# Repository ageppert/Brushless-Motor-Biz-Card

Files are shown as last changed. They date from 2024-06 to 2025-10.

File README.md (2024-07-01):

# Brushless-Motor-Biz-Card
Wind your own brushless motor and experiment in the form factor of a business card!

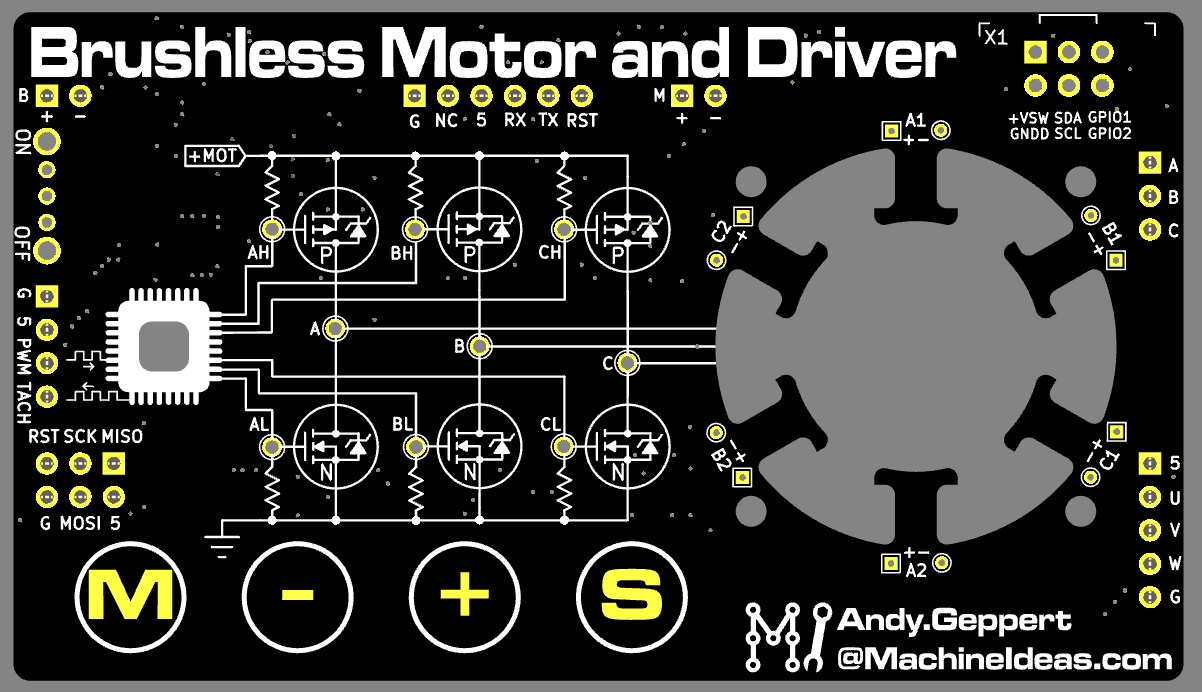
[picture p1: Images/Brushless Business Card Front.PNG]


Follow this project at: https://hackaday.io/project/196576-brushless-motor-and-driver-business-card-kit

# Hardware Version History (latest on top)

HWV0.1 - Prototypes

# REFERENCES

Carl Bugeja - PCB Motors and related magical creations

https://www.youtube.com/@CarlBugeja

Random Access Projects - Open loop brushless motor and beyond

https://www.youtube.com/channel/UCRd9x4pmbc09_RXTrkSY2Gg

Electronoobs - brushless motor and ESC projects

https://www.youtube.com/@ELECTRONOOBS

SimpleFOC Project

https://simplefoc.com/

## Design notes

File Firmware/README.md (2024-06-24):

# Firmware Development

Arduino IDE

5V FTDI-USB Cable

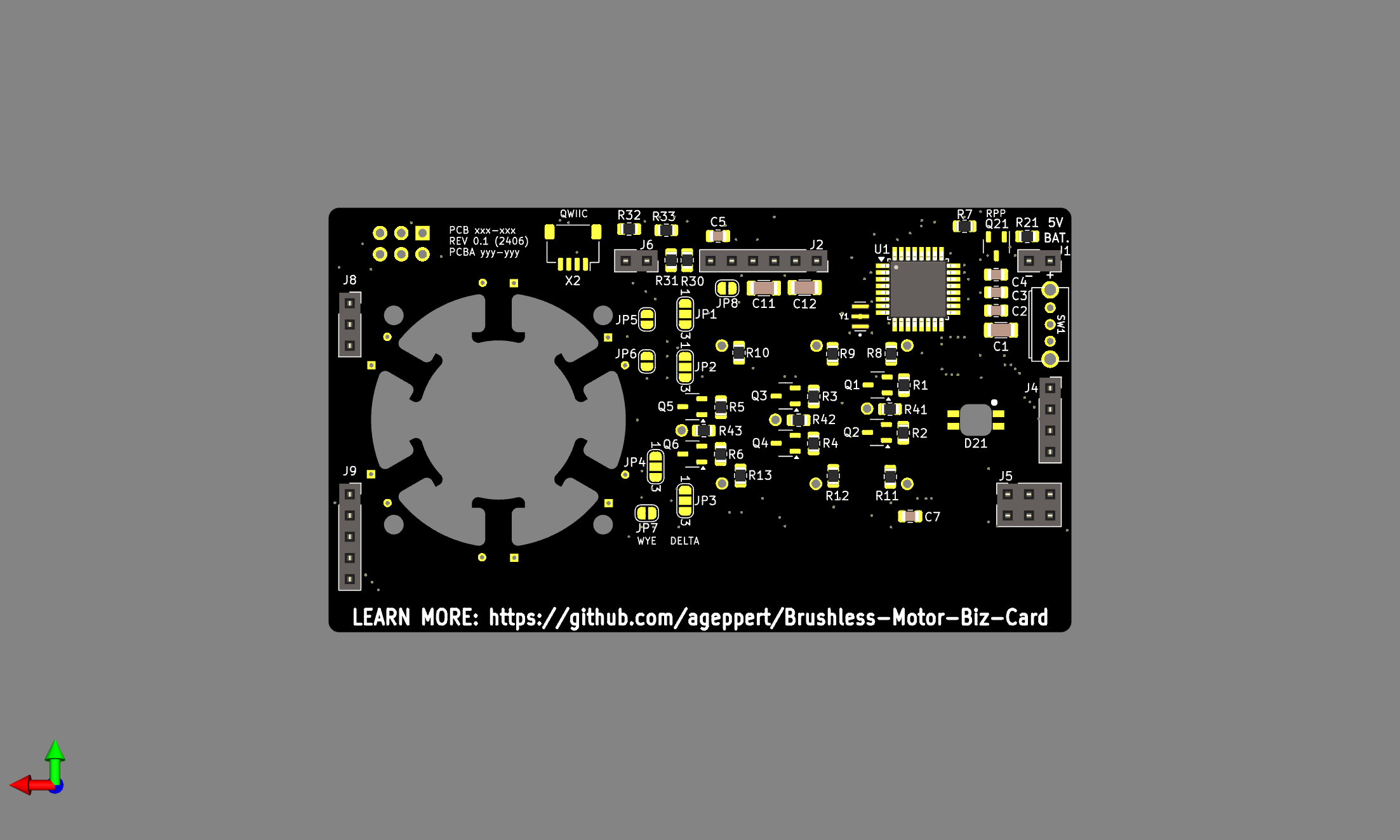
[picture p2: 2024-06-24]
Electronics/BLDC_BIZ_CARD_V0.1 Schematic and Renders/BLDC_BIZ_CARD_render back.png

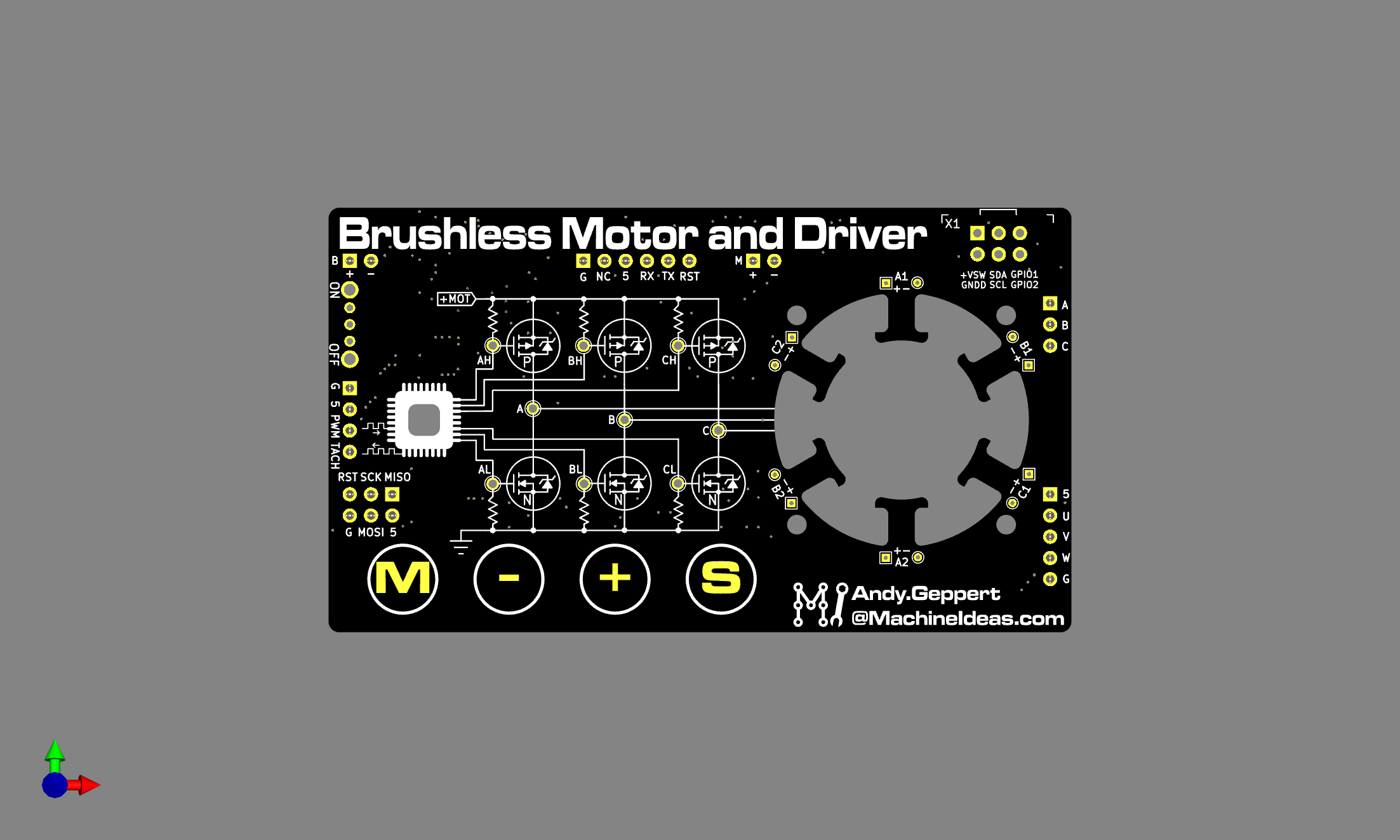
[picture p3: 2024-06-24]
Electronics/BLDC_BIZ_CARD_V0.1 Schematic and Renders/BLDC_BIZ_CARD_render front.png

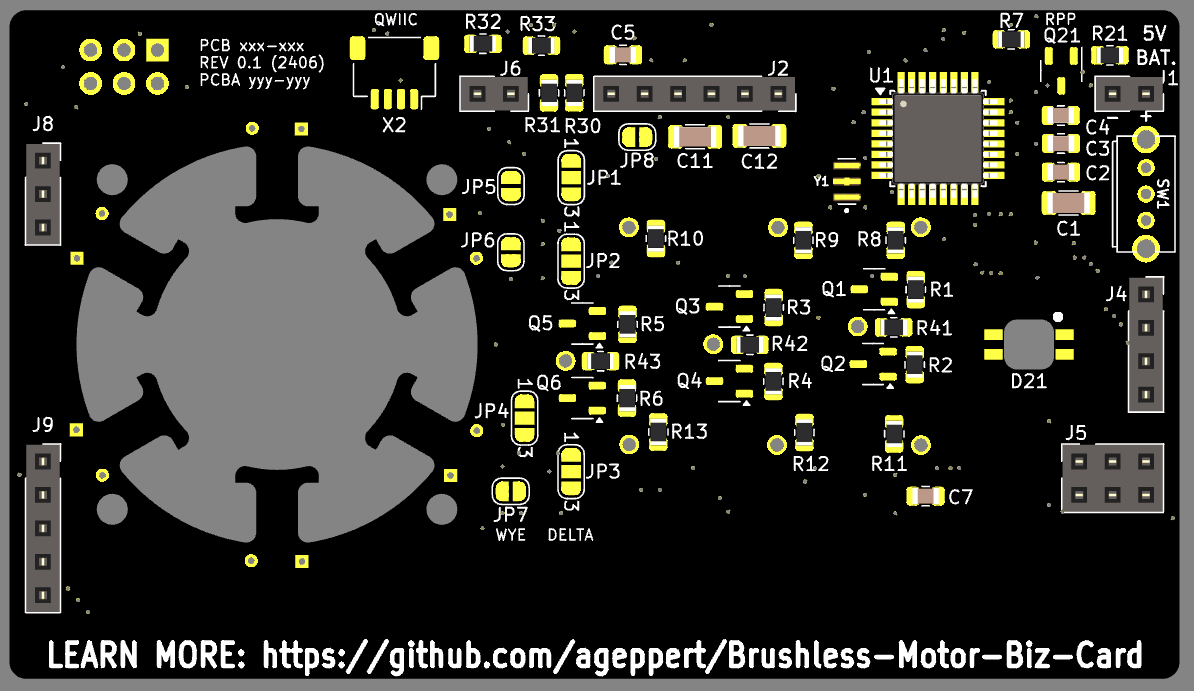
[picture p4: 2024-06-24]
Images/Brushless Business Card Back.PNG

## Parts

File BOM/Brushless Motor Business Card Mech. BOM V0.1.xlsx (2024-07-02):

Brushless Motor and Driver Business Card
Designed by Andy Geppert, www.MachineIdeas.com
Revision 0.1
Mechanical BOM
NAME | DESCRIPTION | QUANTITY | NOTES | LINK
Business Card PCBA | Circuit Board Assembly | 1 | Order a PCB from PCBWAY or JLCPCB with the Gerbers Order the components in the Electrical BOM folder | https://github.com/ageppert/Brushless-Motor-Biz-Card/
Rotor 8P | 3D Print, PETG 0.2mm layers, 20% infill | 1 | DIY, JLCPCB, PCBWAY, etc. | https://cad.onshape.com/documents/f519e018cd04a070474f7458/w/7211a2b8f86f81003258f57c/e/c9c6c988519f346738a797cf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
Motor Support | 3D Print, PETG 0.2mm layers, 20% infill | 4 | DIY, JLCPCB, PCBWAY, etc. | https://cad.onshape.com/documents/f519e018cd04a070474f7458/w/7211a2b8f86f81003258f57c/e/c9c6c988519f346738a797cf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
Winder | 3D Print, PETG 0.2mm layers, 20% infill | 1 | DIY, JLCPCB, PCBWAY, etc. | https://cad.onshape.com/documents/f519e018cd04a070474f7458/w/7211a2b8f86f81003258f57c/e/c9c6c988519f346738a797cf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
Magnet | D22 Cylinder, 1/8" x 1/8" N42, NI. Axial Magnetization | 8 |  | https://www.kjmagnetics.com/proddetail.asp?prod=D22
Bearing | 681X 681X-ZZ Miniature Bearings Mini Open Bearing 1.5 x 4 x 1.2mm | 2 |  | https://www.amazon.com/gp/product/B07HSP9YZ8/
Axle | Brass Rod,Brass Solid Round Rod 0.7mm/0.027inch Diameter, 200mm | 1 | Cut to 0.30 inches | https://www.amazon.com/gp/product/B0B665P1KF
Magnet Wire | 32 AWG enamel or Polyamideimide coating wire | 25 ft | 130 wraps per coil, all coils wind clockwise | https://www.remingtonindustries.com/magnet-wire/magnet-wire-200c-32-awg-polyamideimide-7-spool-sizes/
Screw | M2 x 6mm Phillips head | 4 | Screw assortment comes in handy for other projects! | https://www.amazon.com/gp/product/B0BP6P37QY/

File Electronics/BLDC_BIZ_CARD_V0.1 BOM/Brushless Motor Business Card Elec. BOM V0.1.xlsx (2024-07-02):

Brushless Motor and Driver Business Card
Designed by Andy Geppert, www.MachineIdeas.com
Revision 0.1
REF. DES. | VALUE | FOOTPRINT | QUANTITY | DNP | DIGIKEY PN | MFR PN | OTHER
> C1, C11, C12 | 220uF | Capacitor_SMD:C_1206_3216Metric | 3 |  | 490-13970-1-ND | GRM31CR60J227ME11L
C2 | 10uF | Capacitor_SMD:C_0805_2012Metric | 1 |  | 1276-6472-1-ND | CL21B106KOQNNNG
> C3-C5, C7 | 0.1uF | Capacitor_SMD:C_0805_2012Metric | 4 |  | 1276-2922-1-ND | CL21B104KAFNNNE
D21 | SK6812 | Core_64_footprints:4960_ADA_REV_RGB_LED_short_pads | 1 |  | 1528-4960-ND | SK6812-E
J1 | BATTERY | Connector_PinSocket_2.54mm:PinSocket_1x02_P2.54mm_Vertical | 1 |  | See OTHER |  | Any 0.1" header pins such as: https://www.amazon.com/Header-Lystaii-Pin-Connector-Electronic/dp/B06ZZN8L9S/ https://www.amazon.com/Yohii-Single-Right-Header-Connector/dp/B07C89T16T/
J2 | Conn_01x06_SER_PROG | Connector_PinSocket_2.54mm:PinSocket_1x06_P2.54mm_Vertical | 1 |  | See OTHER
> J4, J9 | Conn_01x04 | -- mixed values -- | 2 |  | See OTHER
J5 | Conn_02x03_Odd_Even_ISP | Connector_PinSocket_2.54mm:PinSocket_2x03_P2.54mm_Vertical | 1 |  | See OTHER
J6 | Conn_01x02_MOTOR_POWER | Connector_PinSocket_2.54mm:PinSocket_1x02_P2.54mm_Vertical | 1 |  | See OTHER
J8 | Conn_01x03 | Connector_PinSocket_2.54mm:PinSocket_1x03_P2.54mm_Vertical | 1 |  | See OTHER
> Q1, Q3, Q5, Q21 | Q_PMOS_GSD | Package_TO_SOT_SMD:SOT-23-3 | 4 |  | DMP2066LSNDICT-ND | DMP2066LSN-7
> Q2, Q4, Q6 | Q_NMOS_GSD | Package_TO_SOT_SMD:SOT-23-3 | 3 |  | DMN2020LSN-7DICT-ND | DMN2020LSN-7
> R1-R6, R41-R43 | 1K | Resistor_SMD:R_0805_2012Metric | 9 |  | 2019-RK73H2ATTD1001FCT-ND | RK73H2ATTD1001F
> R7, R21 | 10K | Resistor_SMD:R_0805_2012Metric | 2 |  | 2019-RK73H2ATTD1002FCT-ND | RK73H2ATTD1002F
> R8-R13 | 470 | Resistor_SMD:R_0805_2012Metric | 6 |  | 2019-RK73H2ATTD4700FCT-ND | RK73H2ATTD4700F
> R30, R31 | 1K2 | Resistor_SMD:R_0805_2012Metric | 2 |  | 2019-RK73H2ATTD1201FCT-ND | RK73H2ATTD1201F
> R32, R33 | 68 | Resistor_SMD:R_0805_2012Metric | 2 |  | 2019-RK73H2ATTD68R0FCT-ND | RK73H2ATTD68R0F
SW1 | SK12D07L4B | BLDC_BIZ_CARD_Footprints:SK12D07VG4 | 1 |  | CKN9559-ND | OS102011MA1QN1
U1 | ATmega328PB-A | Package_QFP:TQFP-32_7x7mm_P0.8mm | 1 |  | ATMEGA328PB-AU-ND | ATMEGA328PB-AU
X1 | SAO_Header | BLDC_BIZ_CARD_Footprints:Badgelife-SAOv169-BADGE-2x3 | 1 |  | S9717-ND | SFH11-NBPC-D03-ST-BK
X2 | QWIIC | Connector_JST:JST_SH_SM04B-SRSS-TB_1x04-1MP_P1.00mm_Horizontal | 1 |  | 455-SM04B-SRSS-TBTR-ND | SM04B-SRSS-TB
Y1 | 16MHz 15pF Resonator | BLDC_BIZ_CARD_Footprints:OSC_CSTNE20M0V53Z000R0 | 1 |  | 490-17950-1-ND | CSTNE16M0V53Z000R0

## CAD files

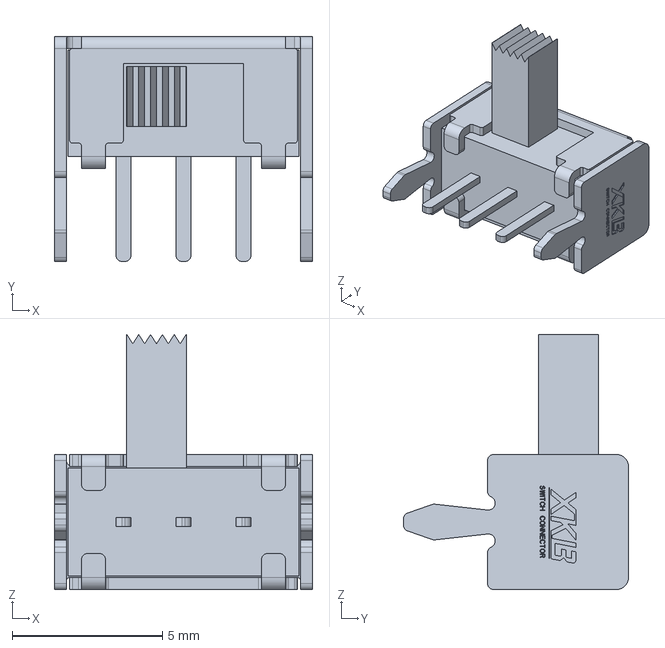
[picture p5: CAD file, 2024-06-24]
Electronics/BLDC_BIZ_CARD_Footprints/SK12D07L4B.stp
8.60 x 7.50 x 8.50 mm

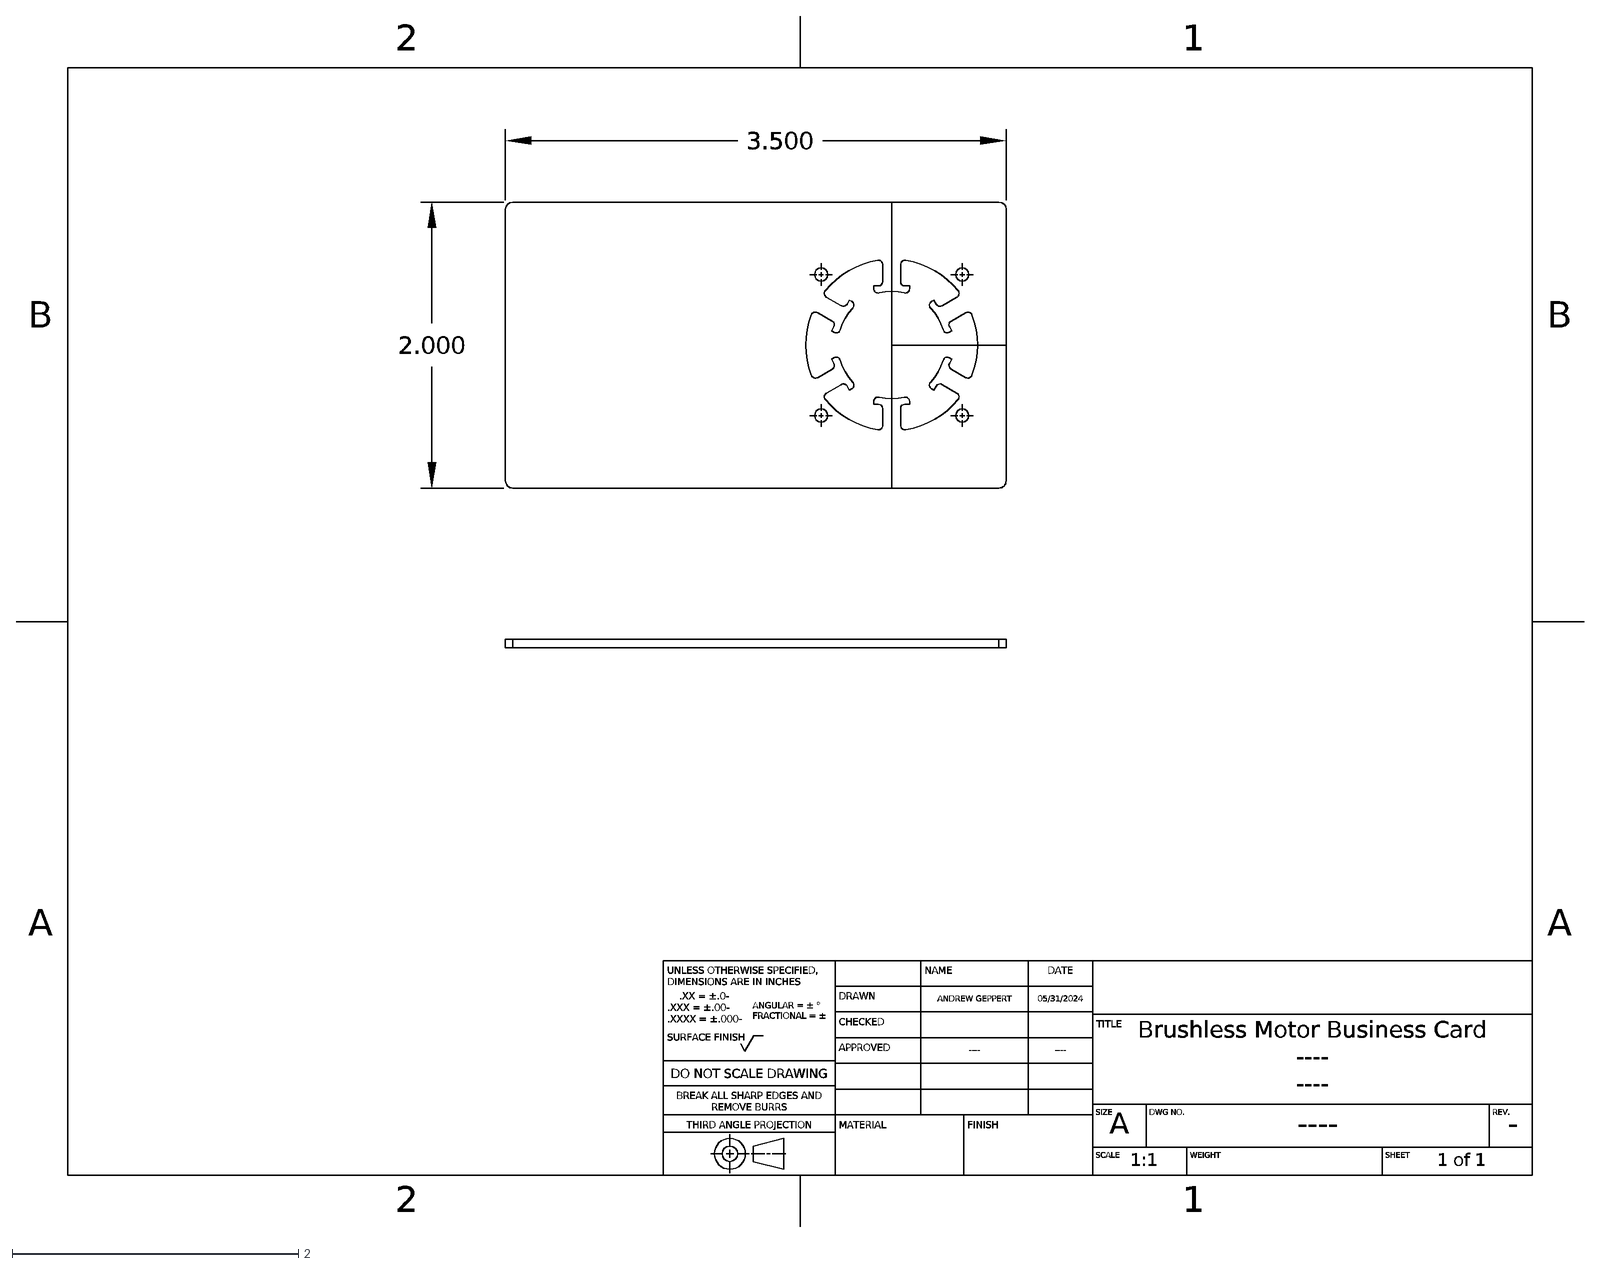
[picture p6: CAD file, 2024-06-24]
Graphics/Card and winding outline.dxf
2
1
A
B
UNLESS OTHERWISE SPECIFIED, DIMENSIONS ARE IN INCHES
.XX = ±.0- .XXX = ±.00- .XXXX = ±.000-
ANGULAR = ± ° FRACTIONAL = ±
SURFACE FINISH
DO NOT SCALE DRAWING
BREAK ALL SHARP EDGES AND REMOVE BURRS
THIRD ANGLE PROJECTION
NAME
DATE
DRAWN
ANDREW GEPPERT
05/31/2024
CHECKED
APPROVED
----
MATERIAL
FINISH
TITLE
Brushless Motor Business Card
SIZE
DWG NO.
REV.
-
SCALE
1:1
WEIGHT
SHEET
1 of 1
3.500
2.000

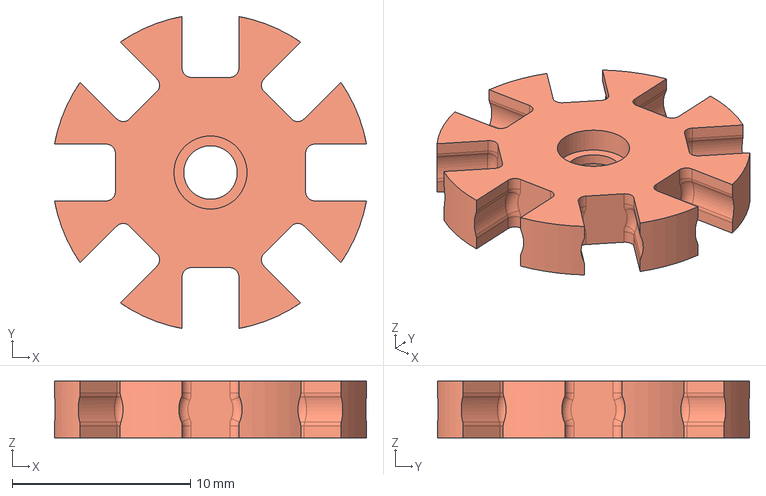
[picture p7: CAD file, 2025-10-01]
Mechanical/Rotor 8P V1.step
17.5 x 17.5 x 3.17 mm

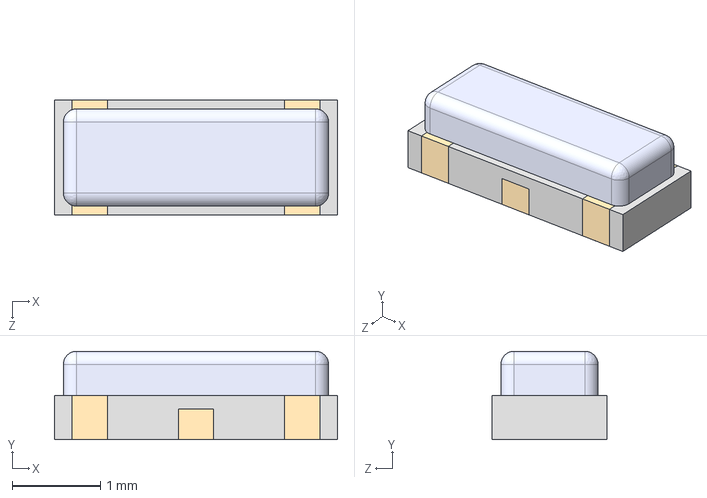
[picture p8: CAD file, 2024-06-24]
Electronics/BLDC_BIZ_CARD_Footprints/OSC_CSTNE20M0V53Z000R0.step
3.20 x 1.00 x 1.30 mm

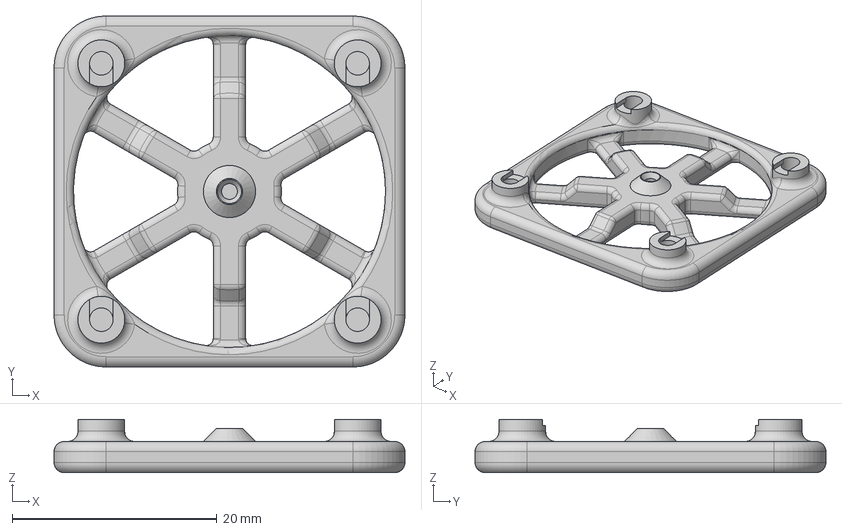
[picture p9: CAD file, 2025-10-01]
Mechanical/Motor Support V1.step
34.3 x 34.3 x 5.21 mm

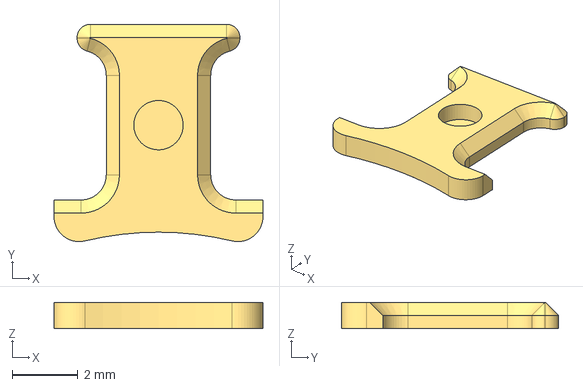
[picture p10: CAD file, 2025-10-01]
Mechanical/Winding Spacer V1.step
6.35 x 6.60 x 0.794 mm

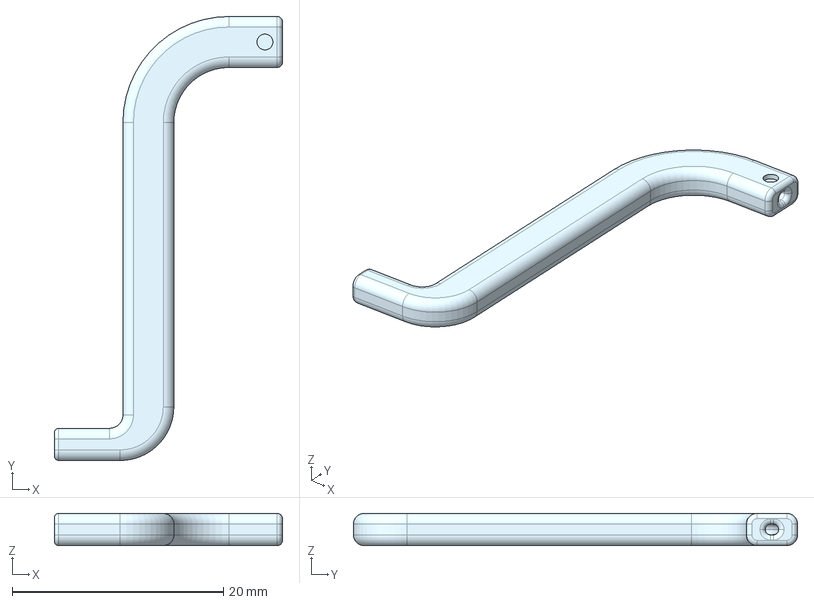
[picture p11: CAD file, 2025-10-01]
Mechanical/Winder V1.step
21.6 x 42.0 x 3.05 mm

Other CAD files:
Mechanical/Motor Support V1.stl
Mechanical/Rotor 8P V1.stl
Mechanical/Winder V1.stl
Mechanical/Winding Spacer V1.stl

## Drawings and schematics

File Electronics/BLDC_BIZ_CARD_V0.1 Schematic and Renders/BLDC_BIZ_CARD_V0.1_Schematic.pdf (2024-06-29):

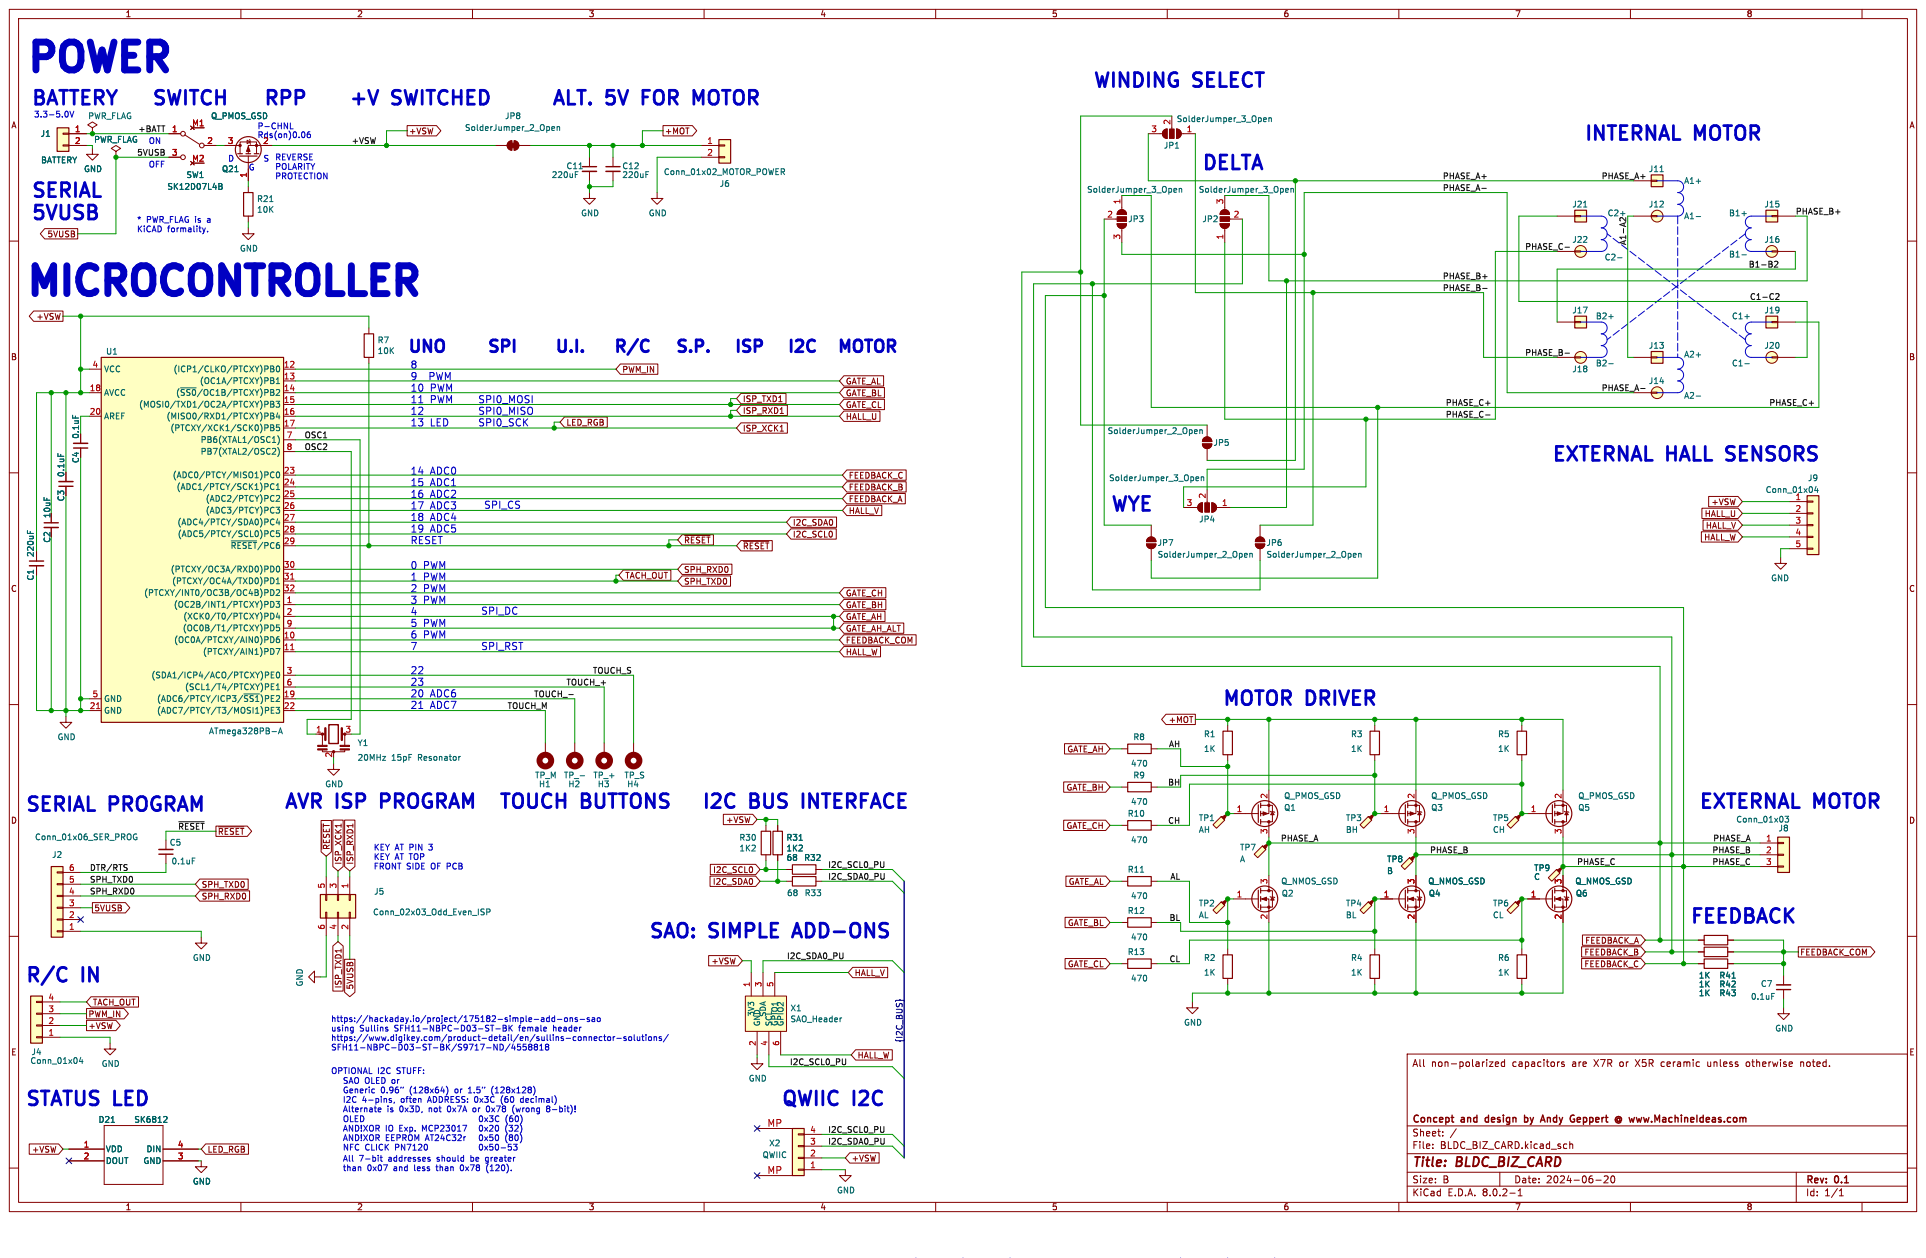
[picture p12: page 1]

KEY AT PIN 3 KEY AT TOP

https://hackaday.io/project/175182-simple-add-ons-sao

AND!XOR IO Exp. MCP23017 AND!XOR EEPROM AT24C32r NFC CLICK PN7120

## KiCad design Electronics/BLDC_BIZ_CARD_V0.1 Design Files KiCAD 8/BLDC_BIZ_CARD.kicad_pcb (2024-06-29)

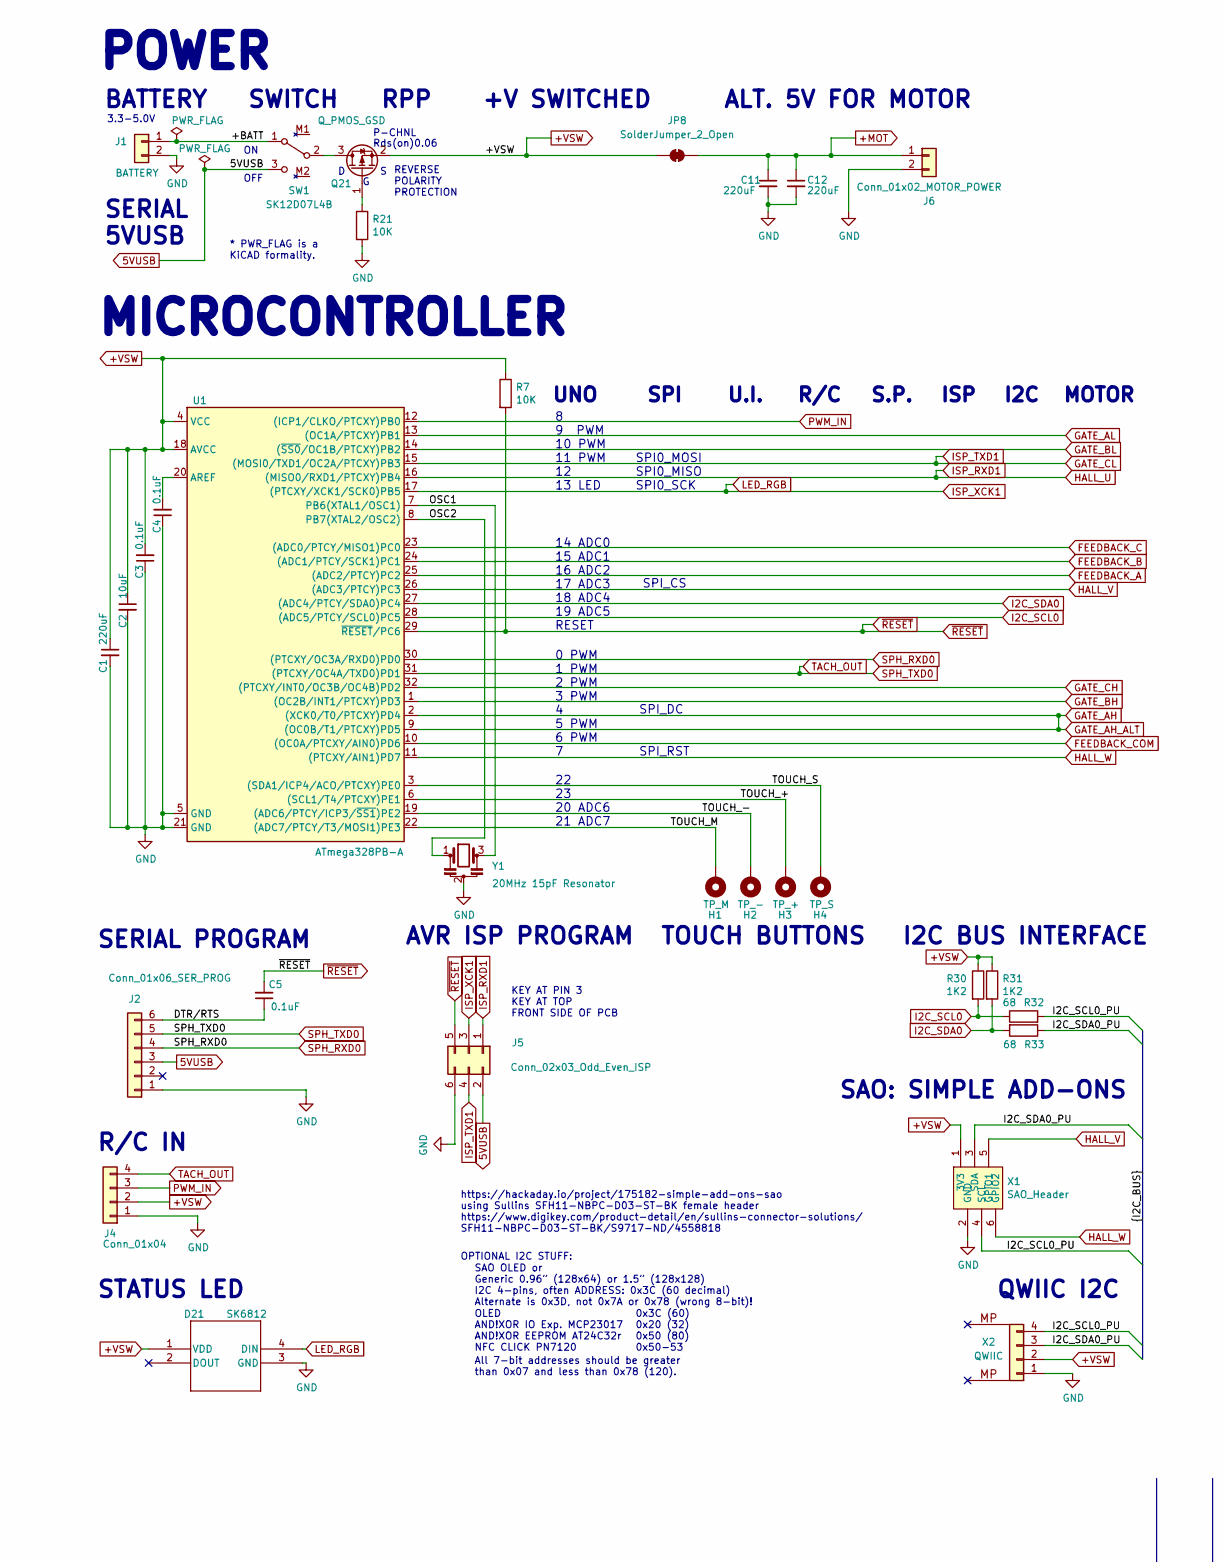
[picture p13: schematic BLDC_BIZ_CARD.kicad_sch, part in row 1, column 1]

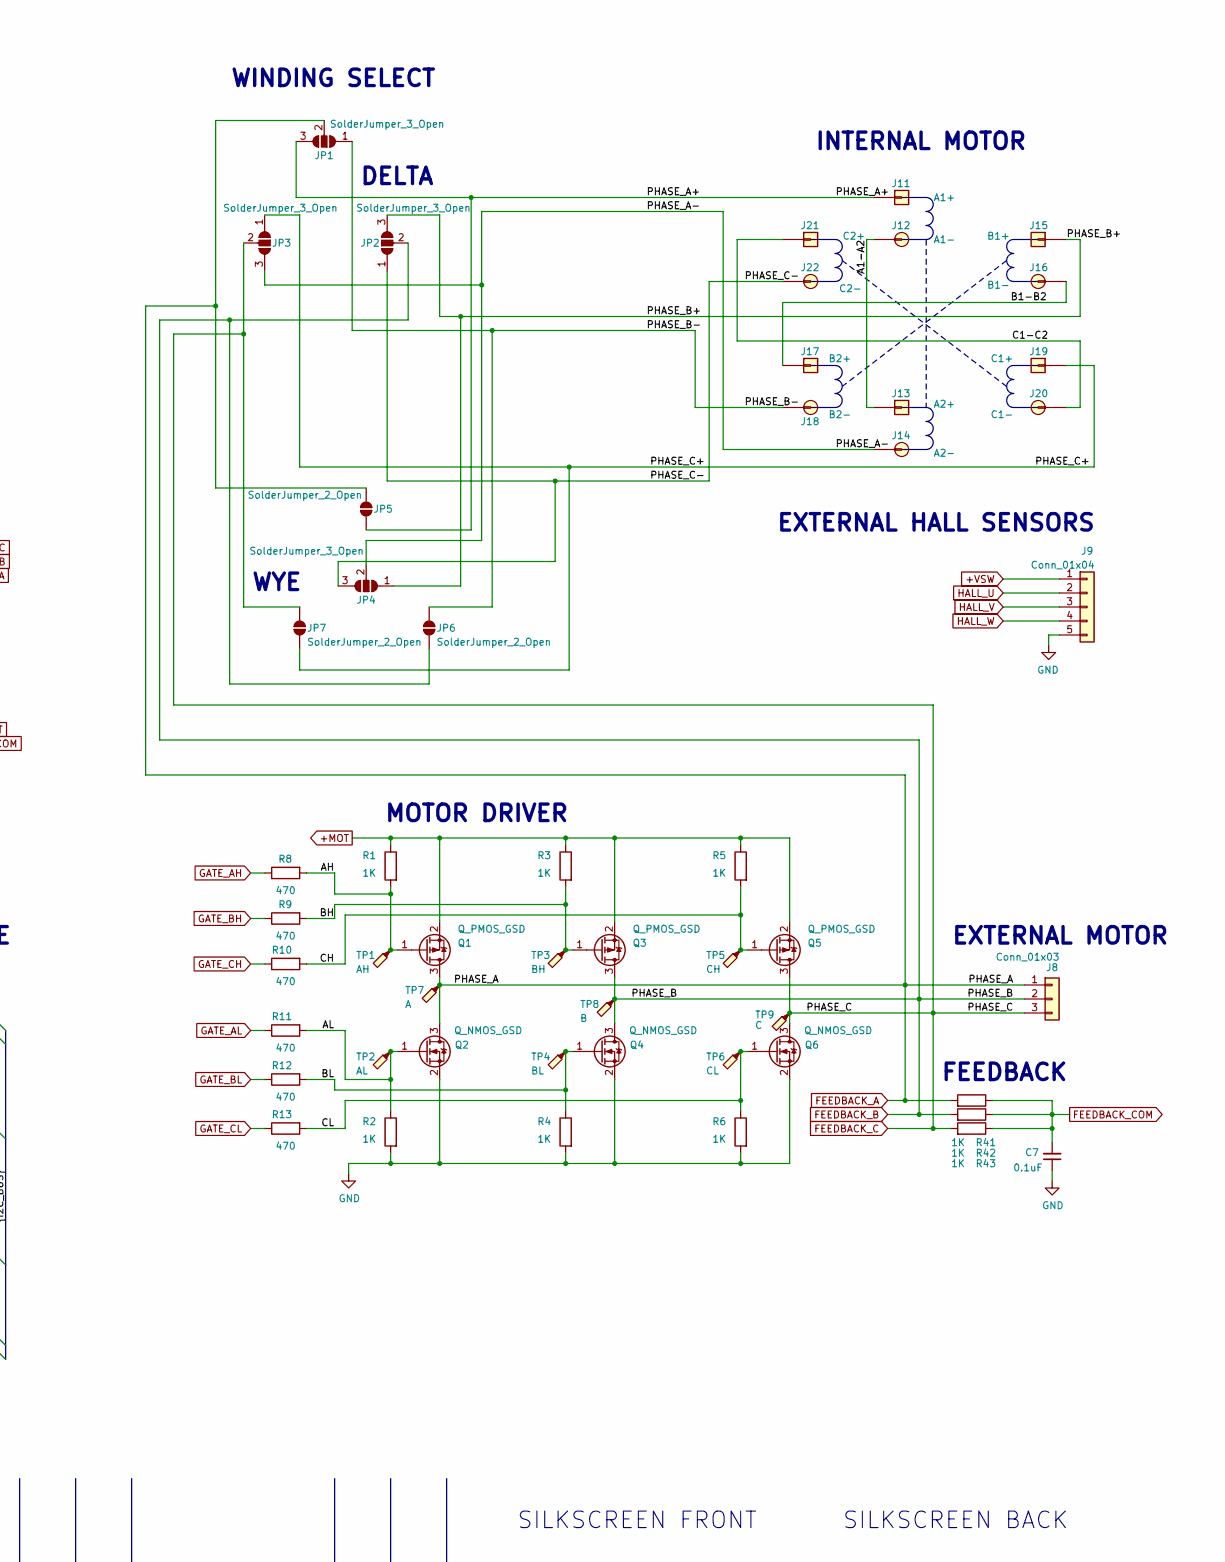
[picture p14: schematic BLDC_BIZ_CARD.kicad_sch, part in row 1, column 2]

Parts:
C1, C11, C12: 220uF; C_1206_3216Metric; LCSC C412252
C2: 10uF; C_0805_2012Metric; LCSC C17024
C3, C4, C5, C7: 0.1uF; C_0805_2012Metric; LCSC C28233
D21: SK6812; 4960_ADA_REV_RGB_LED_short_pads; MPN SK6812-E; Digi-Key_PN 1528-4960-ND
H1: TP_M; BIZ_CARD_TOUCH_PAD
H2: TP_-; BIZ_CARD_TOUCH_PAD
H3: TP_+; BIZ_CARD_TOUCH_PAD
H4: TP_S; BIZ_CARD_TOUCH_PAD
J1: BATTERY; PinSocket_1x02_P2.54mm_Vertical
J2: Conn_01x06_SER_PROG; PinSocket_1x06_P2.54mm_Vertical
J4: Conn_01x04; PinSocket_1x04_P2.54mm_Vertical
J5: Conn_02x03_Odd_Even_ISP; PinSocket_2x03_P2.54mm_Vertical
J6: Conn_01x02_MOTOR_POWER; PinSocket_1x02_P2.54mm_Vertical
J8: Conn_01x03; PinSocket_1x03_P2.54mm_Vertical
J9: Conn_01x04; PinSocket_1x05_P2.54mm_Vertical
J11: A1+; TestPoint_THTPad_1.0x1.0mm_Drill0.5mm
J12: A1-; TestPoint_THTPad_D1.0mm_Drill0.5mm
J13: A2+; TestPoint_THTPad_1.0x1.0mm_Drill0.5mm
J14: A2-; TestPoint_THTPad_D1.0mm_Drill0.5mm
J15: B1+; TestPoint_THTPad_1.0x1.0mm_Drill0.5mm
J16: B1-; TestPoint_THTPad_D1.0mm_Drill0.5mm
J17: B2+; TestPoint_THTPad_1.0x1.0mm_Drill0.5mm
J18: B2-; TestPoint_THTPad_D1.0mm_Drill0.5mm
J19: C1+; TestPoint_THTPad_1.0x1.0mm_Drill0.5mm
J20: C1-; TestPoint_THTPad_D1.0mm_Drill0.5mm
J21: C2+; TestPoint_THTPad_1.0x1.0mm_Drill0.5mm
J22: C2-; TestPoint_THTPad_D1.0mm_Drill0.5mm
JP1, JP2, JP3, JP4: SolderJumper_3_Open; SolderJumper-3_P1.3mm_Open_RoundedPad1.0x1.5mm_NumberLabels
JP5, JP6, JP7, JP8: SolderJumper_2_Open; SolderJumper-2_P1.3mm_Open_RoundedPad1.0x1.5mm
Q1, Q3, Q5: Q_PMOS_GSD; SOT-23-3; Digi-Key_PN DMP2066LSNDICT-ND
Q2, Q4, Q6: Q_NMOS_GSD; SOT-23-3; MPN NVTR4503NT1G; LCSC C20917
Q21: Q_PMOS_GSD; SOT-23-3; MPN SL3401A-TP; LCSC C350311
R1, R2, R3, R4, R5, R6, R41, R42, R43: 1K; R_0805_2012Metric; LCSC C17379
R7, R21: 10K; R_0805_2012Metric; LCSC C269724
R8, R9, R10, R11, R12, R13: 470; R_0805_2012Metric; LCSC C17379
R30, R31: 1K2; R_0805_2012Metric; LCSC C17379
R32, R33: 68; R_0805_2012Metric; LCSC C17802
SW1: SK12D07L4B; SK12D07VG4; MPN OS102011MA1QN1; LCSC C480340
TP1: AH; TestPoint_THTPad_D1.5mm_Drill1.0mm
TP2: AL; TestPoint_THTPad_D1.5mm_Drill1.0mm
TP3: BH; TestPoint_THTPad_D1.5mm_Drill1.0mm
TP4: BL; TestPoint_THTPad_D1.5mm_Drill1.0mm
TP5: CH; TestPoint_THTPad_D1.5mm_Drill1.0mm
TP6: CL; TestPoint_THTPad_D1.5mm_Drill1.0mm
TP7: A; TestPoint_THTPad_D1.5mm_Drill1.0mm
TP8: B; TestPoint_THTPad_D1.5mm_Drill1.0mm
TP9: C; TestPoint_THTPad_D1.5mm_Drill1.0mm
U1: ATmega328PB-A; TQFP-32_7x7mm_P0.8mm; LCSC C132230
X1: SAO_Header; Badgelife-SAOv169-BADGE-2x3; MPN SFH11-NBPC-D03-ST-BK; Digi-Key_PN S9717-ND
X2: QWIIC; JST_SH_SM04B-SRSS-TB_1x04-1MP_P1.00mm_Horizontal; MPN SM04B-SRSS-TB; LCSC C160404
Y1: 20MHz 15pF Resonator; OSC_CSTNE20M0V53Z000R0; LCSC C32180

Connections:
5VUSB: J2.3, J5.2, SW1.3 (C)
+MOT: C11.1, C12.1, J6.1, JP8.1 (A), Q1.2 (S), Q3.2 (S), Q5.2 (S), R1.1, R3.1, R5.1
+VSW: C1.1, C2.1, C3.2, D21.1 (VDD), J4.2, J9.1, JP8.2 (B), Q21.2 (S), R7.1, R30.1, R31.1, U1.4 (VCC), U1.18 (AVCC), X1.1 (3V3), X2.2
/+BATT: J1.1, SW1.1 (A)
/A1-A2: J12.1, J13.1
/AH: Q1.1 (G), R1.2, R8.2, TP1.1
/AL: Q2.1 (G), R2.1, R11.2, TP2.1
/B1-B2: J16.1, J17.1
/BH: Q3.1 (G), R3.2, R9.2, TP3.1
/BL: Q4.1 (G), R4.1, R12.2, TP4.1
/C1-C2: J20.1, J21.1
/CH: Q5.1 (G), R5.2, R10.2, TP5.1
/CL: Q6.1 (G), R6.1, R13.2, TP6.1
/DTR/RTS: C5.1, J2.6
/I2C_SCL0_PU: R32.2, X1.4 (SCL), X2.4
/I2C_SDA0_PU: R33.1, X1.3 (SDA), X2.3
/OSC1: U1.7 (PB6(XTAL1/OSC1)), Y1.3
/OSC2: U1.8 (PB7(XTAL2/OSC2)), Y1.1
/PHASE_A+: J11.1, JP1.3 (B), JP5.1 (A)
/PHASE_A-: J14.1, JP3.3 (B), JP4.2 (C)
/PHASE_B+: J15.1, JP2.3 (B), JP4.1 (A)
/PHASE_B-: J18.1, JP1.1 (A), JP6.2 (B)
/PHASE_C+: J19.1, JP3.1 (A), JP7.1 (A)
/PHASE_C-: J22.1, JP2.1 (A), JP4.3 (B)
/TOUCH_+: H3.1, U1.6 ((SCL1/T4/PTCXY)PE1)
/TOUCH_-: H2.1, U1.19 ((ADC6/PTCY/ICP3/~SS1)PE2)
/TOUCH_M: H1.1, U1.22 ((ADC7/PTCY/T3/MOSI1)PE3)
/TOUCH_S: H4.1, U1.3 ((SDA1/ICP4/ACO/PTCXY)PE0)
FEEDBACK_A: J8.1, JP1.2 (C), JP5.2 (B), Q1.3 (D), Q2.3 (D), R41.2, TP7.1, U1.25 ((ADC2/PTCY)PC2)
FEEDBACK_B: J8.2, JP2.2 (C), JP6.1 (A), Q3.3 (D), Q4.3 (D), R42.2, TP8.1, U1.24 ((ADC1/PTCY/SCK1)PC1)
FEEDBACK_C: J8.3, JP3.2 (C), JP7.2 (B), Q5.3 (D), Q6.3 (D), R43.2, TP9.1, U1.23 ((ADC0/PTCY/MISO1)PC0)
FEEDBACK_COM: C7.2, R41.1, R42.1, R43.1, U1.10 ((OC0A/PTCXY/AIN0)PD6)
GATE_AH: R8.1, U1.2 ((XCK0/T0/PTCXY)PD4), U1.9 ((OC0B/T1/PTCXY)PD5)
GATE_AL: R11.1, U1.13 ((OC1A/PTCXY)PB1)
GATE_BH: R9.1, U1.1 ((OC2B/INT1/PTCXY)PD3)
GATE_BL: R12.1, U1.14 ((~SS0/OC1B/PTCXY)PB2)
GATE_CH: R10.1, U1.32 ((PTCXY/INT0/OC3B/OC4B)PD2)
GATE_CL: J5.4, R13.1, U1.15 ((MOSI0/TXD1/OC2A/PTCXY)PB3)
GND: C1.2, C2.2, C3.1, C4.1, C7.1, C11.2, C12.2, D21.3 (GND), J1.2, J2.1, J4.1, J5.6, J6.2, J9.5, Q2.2 (S), Q4.2 (S), Q6.2 (S), R2.2, R4.2, R6.2, R21.2, U1.5 (GND), U1.21 (GND), X1.2 (GND), X2.1, Y1.2
HALL_U: J5.1, J9.2, U1.16 ((MISO0/RXD1/PTCXY)PB4)
HALL_V: J9.3, U1.26 ((ADC3/PTCY)PC3), X1.5 (GPIO1)
HALL_W: J9.4, U1.11 ((PTCXY/AIN1)PD7), X1.6 (GPIO2)
I2C_SCL0: R30.2, R32.1, U1.28 ((ADC5/PTCY/SCL0)PC5)
I2C_SDA0: R31.2, R33.2, U1.27 ((ADC4/PTCY/SDA0)PC4)
ISP_XCK1: D21.4 (DIN), J5.3, U1.17 ((PTCXY/XCK1/SCK0)PB5)
unnamed: Q21.3 (D), SW1.2 (B)
unnamed: Q21.1 (G), R21.1
unnamed: C4.2, U1.20 (AREF)
PWM_IN: J4.3, U1.12 ((ICP1/CLKO/PTCXY)PB0)
SPH_RXD0: J2.4, U1.30 ((PTCXY/OC3A/RXD0)PD0)
SPH_TXD0: J2.5, J4.4, U1.31 ((PTCXY/OC4A/TXD0)PD1)
~RESET: C5.2, J5.5, R7.2, U1.29 (~RESET/PC6)

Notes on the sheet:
SILKSCREEN FRONT
OLED AND!XOR IO Exp. MCP23017 AND!XOR EEPROM AT24C32r NFC CLICK PN7120
P-CHNL
WYE
EXTERNAL MOTOR
https://hackaday.io/project/175182-simple-add-ons-sao using Sullins SFH11-NBPC-D03-ST-BK female header https://www.digikey.com/product-detail/en/sullins-connector-solutions/ SFH11-NBPC-D03-ST-BK/S9717-ND/4558818
SAO: SIMPLE ADD-ONS
MOTOR
SPI_RST
R/C
AVR ISP PROGRAM
MICROCONTROLLER
0 PWM 1 PWM 2 PWM 3 PWM 4 5 PWM 6 PWM 7
I2C
WINDING SELECT
22 23 20 ADC6 21 ADC7
OFF
UNO
* PWR_FLAG is a KiCAD formality.
SWITCH
DELTA
SAO OLED or Generic 0.96” (128x64) or 1.5” (128x128) I2C 4-pins, often ADDRESS: 0x3C (60 decimal) Alternate is 0x3D, not 0x7A or 0x78 (wrong 8-bit)!
POWER
SPI0_MOSI SPI0_MISO SPI0_SCK
ALT. 5V FOR MOTOR
REVERSE POLARITY PROTECTION
MOTOR DRIVER
U.I.
ISP
SERIAL PROGRAM
Rds(on)0.06
RPP
SPI_DC
8 9 PWM 10 PWM 11 PWM 12 13 LED
S.P.
STATUS LED
KEY AT PIN 3 KEY AT TOP FRONT SIDE OF PCB
BATTERY
SPI
SPI_CS

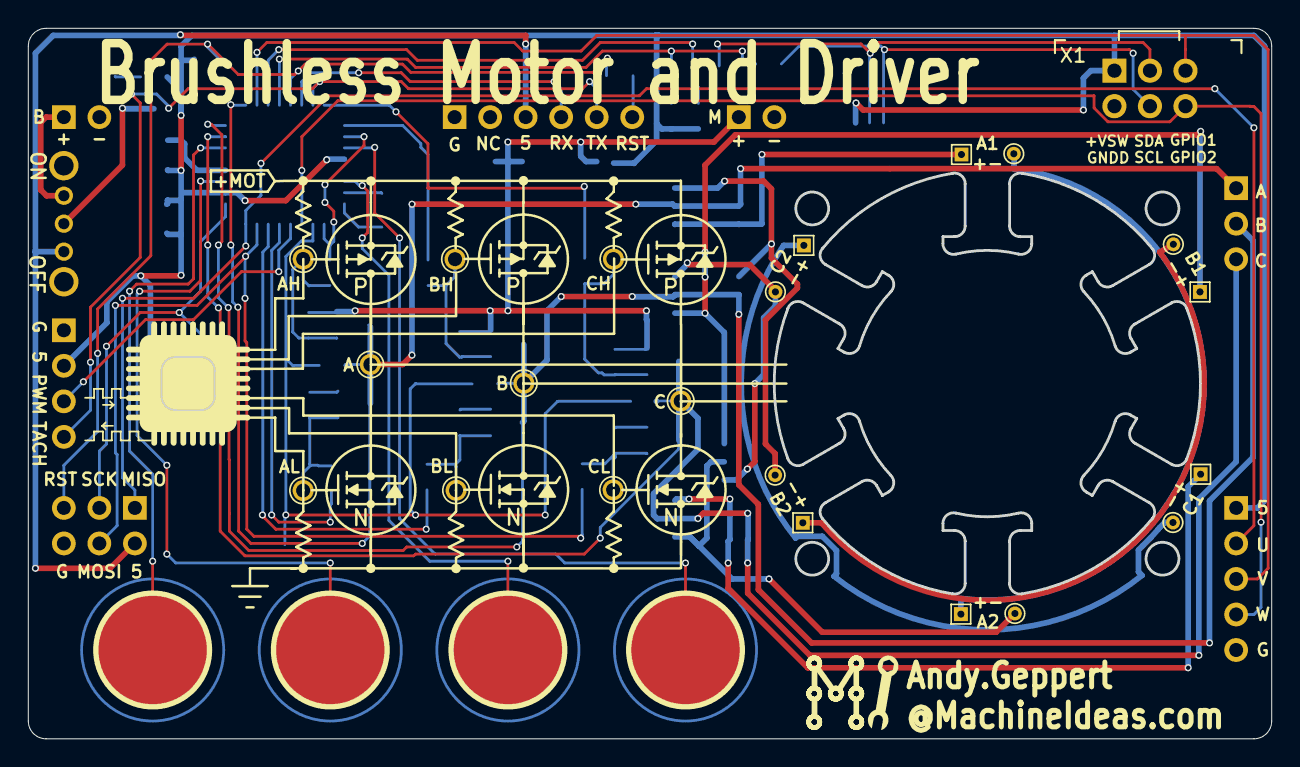
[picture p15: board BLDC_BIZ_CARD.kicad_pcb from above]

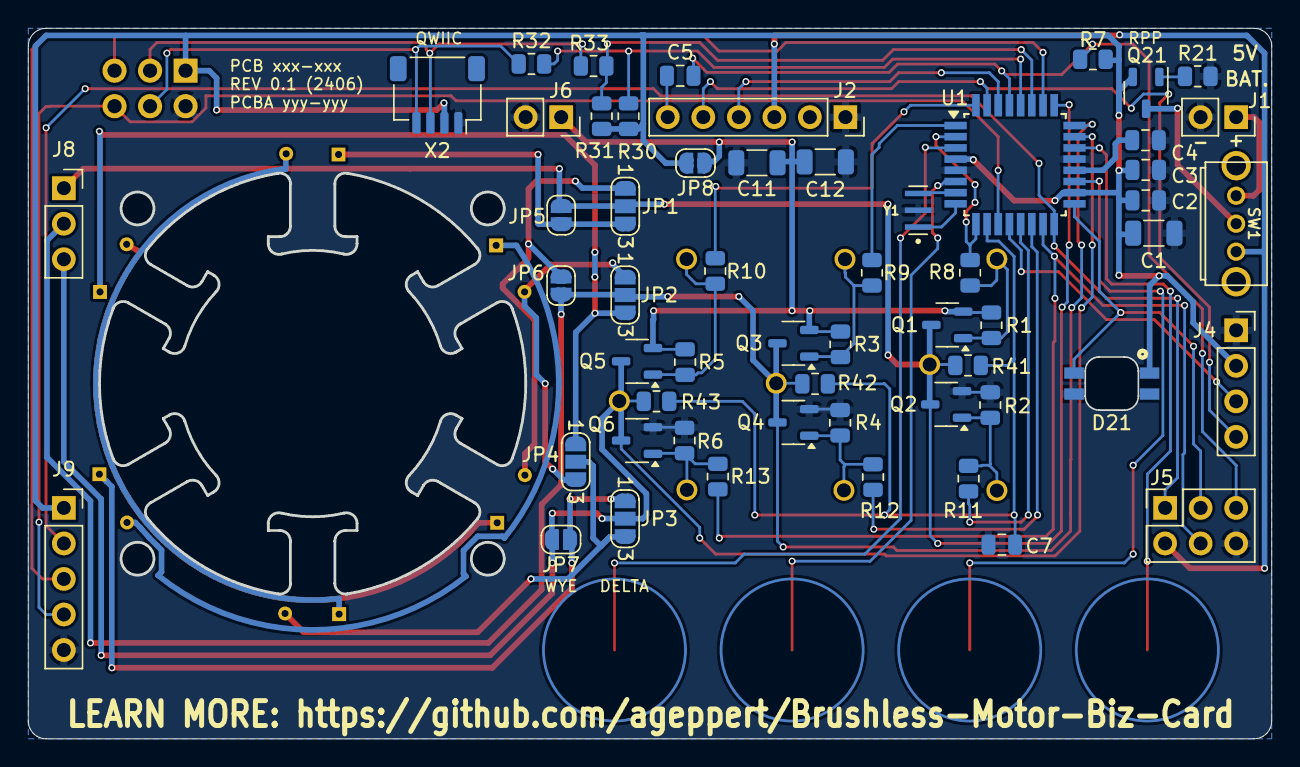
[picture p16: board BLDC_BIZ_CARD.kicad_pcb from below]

Board: 2 copper layers, 88.9 x 50.8 mm, 82 parts (55 on the bottom side), 52 nets.

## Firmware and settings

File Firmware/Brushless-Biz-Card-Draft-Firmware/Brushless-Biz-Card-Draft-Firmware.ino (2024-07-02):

/*    
    Brushless Motor and Driver Business Card
    Andy Geppert, Machine Ideas, June 2024
    V0.1 board, S/N 1
    https://hackaday.io/project/196576-brushless-motor-and-driver-business-card-kit
    https://github.com/ageppert/Brushless-Motor-Biz-Card
      
    Using 328PB from Arduino Uno clone, 16 MHz resonator
    Additional Boards Manager URL: https://mcudude.github.io/MiniCore/package_MCUdude_MiniCore_index.json
    https://github.com/MCUdude/MiniCore?tab=readme-ov-file
    Arduino IDE 1.8.19 / Board / MiniCore / AtMega 328
    Variant PB

    Code started life as:
      Program to run a brushless motor in open loop mode, three approximated sine wave PWM sequences, 120 degrees out of phase
      By Juan Pablo Angulo https://www.patreon.com/randomaccessprojects
      ST L6234 Brushless Driver (like SimpleFOC shield). Three PWM outputs to control high and low side FETs. When high, high side FET is enabled. When low, low side FET is enabled.
    Hacked a bunch by Andy Geppert for Brushless Motor and Driver Business Card
*/

#define DEBUG 0

// USER RGB LED
  #define PIN_LED_GRB   13
  #include <Adafruit_NeoPixel.h>
  #define NUM_LEDS       1
  Adafruit_NeoPixel pixels(NUM_LEDS, PIN_LED_GRB, NEO_GRB + NEO_KHZ800);
  uint8_t  ledBlinkState = 0;
  uint32_t previousMillis = 0;
  uint32_t currentMillis = 0;
  const long interval = 500;

// SAO OLED I2C 0x3C
  #include <Wire.h>
  #include <Adafruit_GFX.h>
  #include <Adafruit_SSD1306.h>
  #define SCREEN_WIDTH 128 // OLED display width, in pixels
  #define SCREEN_HEIGHT 64 // OLED display height, in pixels
  // Declaration for an SSD1306 display connected to I2C (SDA, SCL pins)
  // On an arduino UNO:       A4(SDA), A5(SCL)
  #define OLED_RESET     -1 // Reset pin # (or -1 if sharing Arduino reset pin)
  #define SCREEN_ADDRESS 0x3C
  Adafruit_SSD1306 display(SCREEN_WIDTH, SCREEN_HEIGHT, &Wire, OLED_RESET);

// PWM
  uint8_t pinGateAH =  5;         // Set high to disable upper PFET, low to enable.
  uint8_t pinGateBH =  3;
  uint8_t pinGateCH =  2;
  uint8_t pinGateAL =  9;         // Set low to disable lower NFET, high to enable.
  uint8_t pinGateBL = 10;
  uint8_t pinGateCL = 11;

// MOTOR CONTROL Variables
  #define POWER_SCALAR 1          // Between 0 and 1 to reduce the peak PWM value, aka voltage.
  uint32_t stepDelay = 1000;          // Number of milliseconds between steps through the electrical cycle sine array

  // STARTED WITH 73 ELEMENTS, BACK TO BACK SINE WAVES.
  int16_t pwmSinePosNeg[] = {0,22,44,65,87,107,127,146,163,180,195,208,220,231,239,246,251,254,255,254,251,246,239,231,220,208,195,180,163,146,127,107,87,65,44,22,0,-23,-45,-66,-88,-108,-128,-147,-164,-181,-196,-209,-221,-232,-240,-247,-252,-255,-255,-255,-252,-247,-240,-232,-221,-209,-196,-181,-164,-147,-128,-108,-88,-66,-45,-23,-1};
  // TESTING WITH 36 MORE ELEMENTS, PRE-PENDED ZEROS.
  // int16_t pwmSinePosNeg[] = {0,0,0,0,0,0,0,0,0,0,0,0,0,0,0,0,0,0,0,0,0,0,0,0,0,0,0,0,0,0,0,0,0,0,0,  0,22,44,65,87,107,127,146,163,180,195,208,220,231,239,246,251,254,255,254,251,246,239,231,220,208,195,180,163,146,127,107,87,65,44,22,0,-23,-45,-66,-88,-108,-128,-147,-164,-181,-196,-209,-221,-232,-240,-247,-252,-255,-255,-255,-252,-247,-240,-232,-221,-209,-196,-181,-164,-147,-128,-108,-88,-66,-45,-23,-1};
  uint8_t SineArrayElementCount = sizeof(pwmSinePosNeg) / sizeof(pwmSinePosNeg[0]);
  uint8_t currentStepA  =                (SineArrayElementCount *  90 / 360);  // initial array position at 90 degrees for coil A
  uint8_t currentStepB  = currentStepA + (SineArrayElementCount * 120 / 360);  // initial array position at 90 + 120 = 210 degrees for coil B
  uint8_t currentStepC  = currentStepB + (SineArrayElementCount * 120 / 360);  // initial array position at 90 + 240 = 330 degrees for coil C

void setup() {
  // Serial Port
    Serial.begin(115200);
  // EEPROM built in to AT328PB

  // LEDs
    pixels.begin();
    pixels.clear();
    pixels.show();
    ledGreen();
    delay(500);

  // Detect board type through built-in MCU EEPROM
  
  // Configure hardware per EEPROM
    // Default state of pins should be floating, and external (on-board) hardware should provide safe starting states
    // Inputs

    // Capacitive touch buttons

    // PWM Frequency, assuming ATmega 328PB at 16 MHz.
      TCCR0B = TCCR0B & 0b11111000 | 0x01; // Pins 5 (AH) & 6 (FEEDBACK_COM).                              0x03=977 Hz default. Changing this will also affect millis() and delay(), better to leave it default.
      TCCR1B = TCCR1B & 0b11111000 | 0x01; // Pins 9 (AL) & 10 (BL).          0x01=31763 Hz, 0x02=3921 Hz, 0x03=490 Hz default.
      TCCR2B = TCCR2B & 0b11111000 | 0x01; // Pins 3 (BH) & 11 (CL).          0x01=31763 Hz, 0x02=3921 Hz, 0x03= 1 kHz default.
      TCCR4B = TCCR4B & 0b11111000 | 0x01; // Pin  2 (CH)                     0x01=31763 Hz, 0x02=3921 Hz, 0x03=490 Hz default.
      ICR1 = 255 ; // 8 bit resolution for PWM

    // OUTPUT PINS
      pinMode(pinGateAL, OUTPUT);
      pinMode(pinGateBL, OUTPUT);
      pinMode(pinGateCL, OUTPUT);
      pinMode(pinGateAH, OUTPUT);
      pinMode(pinGateBH, OUTPUT);
      pinMode(pinGateCH, OUTPUT);
      // pinModeFast(pinGateAH, OUTPUT);
      // pinModeFast(pinGateBH, OUTPUT);
      // pinModeFast(pinGateCH, OUTPUT);
      pwmAllDisable();

  // OLED SETUP
    // SSD1306_SWITCHCAPVCC = generate display voltage from 3.3V internally
    if(!display.begin(SSD1306_SWITCHCAPVCC, SCREEN_ADDRESS)) {
      Serial.println(F("SSD1306 allocation failed"));
    }
    else {
      display.setTextColor(WHITE);
      display.setTextSize(2);
      display.clearDisplay();
      display.setCursor(0, 0);
      display.println(F(" Brushless"));
      display.println(F("   Motor"));
      display.setCursor(7, 32);
      display.println(F(" Biz Card"));
      display.setTextSize(1);
      display.setCursor(22, 48);
      display.println(F("By Andy Geppert")); 
      display.println(F(" www.MachineIdeas.com")); 
      display.display();      
    }
    ledBlue();
    delay(500);

  // DISPLAY CONFIGURATION PARAMETERS
    Serial.print("Sine Wave Array Element Count: ");
    Serial.println(SineArrayElementCount);
    Serial.print("Sine Wave Array Element Starting Positions (A,B,C): ");
    Serial.print(currentStepA);
    Serial.print(", ");
    Serial.print(currentStepB);
    Serial.print(", ");
    Serial.print(currentStepC);
    Serial.println();
    Serial.print("Sine Wave Array Element Starting PWM Values (A,B,C): ");
    Serial.print(pwmSinePosNeg[currentStepA]);
    Serial.print(", ");
    Serial.print(pwmSinePosNeg[currentStepB]);
    Serial.print(", ");
    Serial.print(pwmSinePosNeg[currentStepC]);
    Serial.println();
    
} // END OF SETUP FUNCTION
 
void loop() {
  // MAIN APPLICATION MODE
    // HOUSEKEEPING
      // Blink to look alive
        currentMillis = millis();
        if (currentMillis - previousMillis >= interval) {
          previousMillis = currentMillis;
          if (ledBlinkState == 0) { ledBlinkState = 1; ledRed();}
          else {ledBlinkState = 0; ledOff(); }
        }
      // check the buttons
      // read the potentiometer (if active)
      // read the PWM input (if active)
      // serial port management
    
    // STATE MANAGER
    // pwmAllDisable();
    // move();
    // phaseABrampUpDownTriangle();
    // phaseABrampUpDownSine(stepDelay);
    // PhaseCLowSideSine(stepDelay);
    spinTheMotorBlindlySineWave(stepDelay);

    // delay (10);
    #if DEBUG == 1
      Serial.print(currentStepA);
      Serial.print(", ");
      Serial.print(currentStepB);
      Serial.print(", ");
      Serial.println(currentStepC);
    #endif    
    
} // END OF MAIN LOOP FUNCTION

void spinTheMotorBlindlyTrapezoidal(uint8_t value)
{
  // Step One
  
}

void spinTheMotorBlindlySineWave(uint8_t value)
{
  /* H-Bridges and 6 step sequence
      AH Q1    BH Q3   CH  Q5  (high side transistors are only on or off, no PWM needed)
          U        V        W
      AL Q2    BL Q4   CL  Q6  (low side transistors are PWM modulated)

  Step  Q1  Q2  Q3  Q4  Q5  Q6
        +   -   +   -   +   -
  1     on          pwm
  2     on                  pwm
  3             on          pwm
  4         pwm on
  5         pwm         on
  6                 pwm on
  */
  currentStepA = currentStepA + 1;  // Once the phasing is set, just increment all of the phases through the array.
  currentStepB = currentStepB + 1;
  currentStepC = currentStepC + 1;
  
  currentStepA = currentStepA % SineArrayElementCount; // Remainder operation or modulo to "wrap" the values between 0 and # of elements in the array.
  currentStepB = currentStepB % SineArrayElementCount;
  currentStepC = currentStepC % SineArrayElementCount;

  SetPwmPhaseA(pwmSinePosNeg[currentStepA]);
  SetPwmPhaseB(pwmSinePosNeg[currentStepB]);
  SetPwmPhaseC(pwmSinePosNeg[currentStepC]);
  #if DEBUG == 2
    Serial.print(pwmSinePosNeg[currentStepA]);
    Serial.print(", ");
    Serial.print(pwmSinePosNeg[currentStepB]);
    Serial.print(", ");
    Serial.print(pwmSinePosNeg[currentStepC]);
    Serial.println();
  #endif
  delay(value);
  delay(value);
  delay(value);
}

void SetPwmPhaseA (int16_t value)
{
  // disable low side, pwm high side, with inverted logic (PWM value 5 converts to 250)
  if ((value > 0) && (value <  256)) {
    digitalWrite(pinGateAL,LOW ); 
    analogWrite(pinGateAH,(255-value) * POWER_SCALAR);
    // Serial.println("     LOW");
    }
  // disable high side, pwm low side, with direct logic (PWM value 5 stays 5)
  if ((value < 0) && (value > -256)) {
    digitalWrite(pinGateAH,HIGH); 
    analogWrite(pinGateAL,abs(value) * POWER_SCALAR);
    // Serial.println("              HIGH)");
    } 
  // disable low and high side
  if (value == 0) { 
    digitalWrite(pinGateAL,LOW ); 
    digitalWrite(pinGateAH,HIGH);
    // Serial.println("                      FLOAT)");
    }
}

void SetPwmPhaseB (int16_t value)
{
  // disable low side, pwm high side, with inverted logic (PWM value 5 converts to 250)
  if ((value > 0) && (value <  256)) {
    digitalWrite(pinGateBL,LOW ); 
    analogWrite(pinGateBH,(255-value) * POWER_SCALAR);
    }
  // disable high side, pwm low side, with direct logic (PWM value 5 stays 5)
  if ((value < 0) && (value > -256)) {
    digitalWrite(pinGateBH,HIGH); 
    analogWrite(pinGateBL,abs(value) * POWER_SCALAR);
    } 
  // disable low and high side
  if (value == 0) { 
    digitalWrite(pinGateBL,LOW ); 
    digitalWrite(pinGateBH,HIGH);
    }
}

void SetPwmPhaseC (int16_t value)
{
  // disable low side, pwm high side, with inverted logic (PWM value 5 converts to 250)
  if ((value > 0) && (value <  256)) {
    digitalWrite(pinGateCL,LOW ); 
    analogWrite(pinGateCH,(255-value) * POWER_SCALAR);
    }
  // disable high side, pwm low side, with direct logic (PWM value 5 stays 5)
  if ((value < 0) && (value > -256)) {
    digitalWrite(pinGateCH,HIGH); 
    analogWrite(pinGateCL,abs(value) * POWER_SCALAR);
    } 
  // disable low and high side
  if (value == 0) { 
    digitalWrite(pinGateCL,LOW ); 
    digitalWrite(pinGateCH,HIGH);
    }
}

void PhaseAHighSideSine(uint8_t value)
{
  for( uint8_t i = 0; i < SineArrayElementCount; i++) {
    analogWrite(pinGateAH,pwmSinePosNeg[i]*POWER_SCALAR);
    delay(value);
  }
  digitalWrite(pinGateAH, HIGH);
}

void PhaseBHighSideSine(uint8_t value)
{
  for( uint8_t i = 0; i < SineArrayElementCount; i++) {
    analogWrite(pinGateBH,pwmSinePosNeg[i]*POWER_SCALAR);
    delay(value);
  }
  digitalWrite(pinGateBH, HIGH);
}

void PhaseCHighSideSine(uint8_t value)
{
  for( uint8_t i = 0; i < SineArrayElementCount; i++) {
    analogWrite(pinGateCH,pwmSinePosNeg[i]*POWER_SCALAR);
    delay(value);
  }
  digitalWrite(pinGateCH, HIGH);
}


void PhaseALowSideSine(uint8_t value)
{
  for( uint8_t i = 0; i < SineArrayElementCount; i++) {
    analogWrite(pinGateAL,pwmSinePosNeg[i]*POWER_SCALAR);
    delay(value);
  }
  digitalWrite(pinGateAL, LOW);
}
void PhaseBLowSideSine(uint8_t value)
{
  for( uint8_t i = 0; i < SineArrayElementCount; i++) {
    analogWrite(pinGateBL,pwmSinePosNeg[i]*POWER_SCALAR);
    delay(value);
  }
  digitalWrite(pinGateBL, LOW);
}

void PhaseCLowSideSine(uint8_t value)
{
  for( uint8_t i = 0; i < SineArrayElementCount; i++) {
    analogWrite(pinGateCL,pwmSinePosNeg[i]*POWER_SCALAR);
    delay(value);
  }
  digitalWrite(pinGateCL, LOW);
}

void phaseABrampUpDownSine(uint8_t value)
{
  for( uint8_t i = 0; i < SineArrayElementCount; i++) {
    pwmAtoBEnable(pwmSinePosNeg[i]);
    delay(value);
  }
  pwmAtoBEnable(0);
}

void phaseABrampUpDownTriangle()
{
  for( uint8_t i = 0; i < 255; i++) {
    pwmAtoBEnable(i);
    delay(1);
  }
  for( uint8_t i = 255; i > 0; i--) {
    pwmAtoBEnable(i);
    delay(1);
  }
  pwmAtoBEnable(0);

  for( uint8_t i = 0; i < 255; i++) {
    pwmBtoAEnable(i);
    delay(1);
  }
  for( uint8_t i = 255; i > 0; i--) {
    pwmBtoAEnable(i);
    delay(1);
  }
  pwmBtoAEnable(0);
}

void pwmAtoBEnable(uint8_t value)
{
  if (value>0) {
    // analogWrite(pinGateAH,0);       // A high side enable solid
    digitalWrite(pinGateAH, LOW);
    analogWrite(pinGateBL,value);   // B low side enable PWM
  }
  else {
    // analogWrite(pinGateAH,255);     // A high side disable solid
    digitalWrite(pinGateAH, HIGH);
    analogWrite(pinGateBL,0);       // B low side disable PWM
  }
}

void pwmBtoAEnable(uint8_t value)
{
  if (value>0) {
    // analogWrite(pinGateBH,0);       // A high side enable solid
    digitalWrite(pinGateBH, LOW);
    analogWrite(pinGateAL,value);   // B low side enable PWM
  }
  else {
    // nalogWrite(pinGateBH,255);     // A high side disable solid
    digitalWrite(pinGateBH, HIGH);
    analogWrite(pinGateAL,0);       // B low side disable PWM
  }
}

void pwmAllDisable()
{
  // analogWrite(pinGateAH,255);
  // analogWrite(pinGateBH,255);
  // analogWrite(pinGateCH,255);
  digitalWrite(pinGateAH, HIGH);
  digitalWrite(pinGateBH, HIGH);
  digitalWrite(pinGateCH, HIGH);
  analogWrite(pinGateAL,0);
  analogWrite(pinGateBL,0);
  analogWrite(pinGateCL,0);  
}

void twinkle()
{
  pixels.setPixelColor(0, pixels.Color(3, 0, 0));
  pixels.show();
  delay(1);
  pixels.setPixelColor(0, pixels.Color(0, 3, 0));
  pixels.show();
  delay(1);
  pixels.setPixelColor(0, pixels.Color(0, 0, 3));
  pixels.show();
  delay(1);
}

void ledOff()
{
  pixels.setPixelColor(0, pixels.Color(0, 0, 0));
  pixels.show();
}

void ledRed()
{
  pixels.setPixelColor(0, pixels.Color(3, 0, 0));
  pixels.show();
}

void ledGreen()
{
  pixels.setPixelColor(0, pixels.Color(0, 3, 0));
  pixels.show();
}

void ledBlue()
{
  pixels.setPixelColor(0, pixels.Color(0, 0, 3));
  pixels.show();
}

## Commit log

2024-06-29 Rotate ISP port on schematic to match board orientation.
    [BLDC_BIZ_CARD.kicad_pcb, BLDC_BIZ_CARD.kicad_sch, BLDC_BIZ_CARD_V0.1_PCBA_BOM.xlsx]
2024-06-29 Twinkle RGB LED and serial port test
2024-06-29 Working I2C and SAO OLED!
2024-06-29 Add LED color modes
    LED Green at start-up. LED Blue during OLED set-up. LED blinking RED whilst looping open loop motor control.
2024-06-29 Increase start-up LED color durations, add schematic OLED note
    [BLDC_BIZ_CARD.kicad_sch]
2024-06-30 PWMing the high sides too
2024-07-02 Add Mech. and Elec. BOMs
    [BLDC_BIZ_CARD.kicad_sch, BLDC_BIZ_CARD_V0.1_PCBA_BOM.xlsx, Brushless Motor Business Card Elec. BOM V0.1.xlsx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]
2024-08-25 Add touch sensor design guide
2025-10-01 Add mechanical parts STEP and STL files V1
    [Motor Support V1.step, Motor Support V1.stl, Rotor 8P V1.step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]
